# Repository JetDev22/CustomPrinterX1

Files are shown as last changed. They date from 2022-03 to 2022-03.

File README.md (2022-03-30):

# CustomPrinter X1
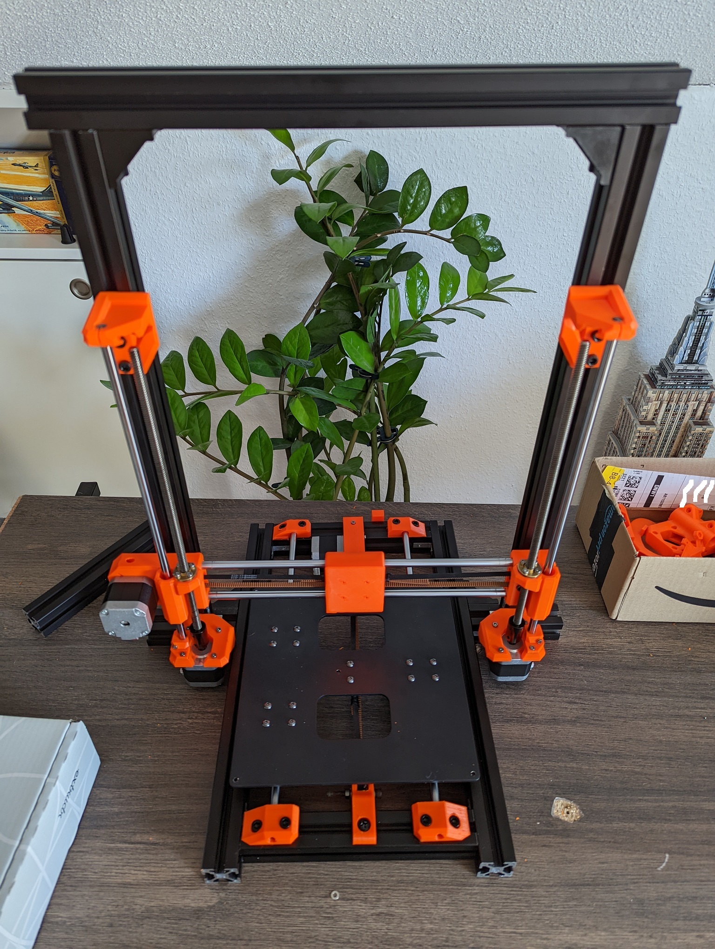
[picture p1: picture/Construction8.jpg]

## The Idea

My Anycubic Mega S was performing quite well for two years, when I suddenly had several kill calls by the firmware due to thermal runaway. I could not isolate the problem. I changed the thermister, heater cartridge, checked the cables .... no change. Sometimes it printed flawless for weeks, other times it stalled several times a day.

So I decided to strip the Mega S for its parts and try to start from scratch, by building my own 3D Printer. The goals where:
- Upgrade to a 32bit board
- Construct a 3030 aluminium extrusion frame, that are intentinally not cut to exact lengths, so the can be used later on
- Add an all metal V6 style Hotend to be able to experiment beyond PETG
- Add a TFT35 display to be able to use the retro-style marlin display, as well as the TFT35 GUI (and customize the GUI)
- Configure Marlin from scratch, to learn more about the firmware and have it fit my printer
- Initially use parts from prusaprinters/thingiverse and replace them, once that printer works reliable, with parts designed by me
- Publish my firmware/parts/ideas/findings on my github to encourage others to do the same or recreate my build

## Parts used from the Anycubic Mega S

The following lists all the parts I reused from disassembling the Mega S:
- Both Z-Axis Nema 17s
- The shorter Extruder NEMA 17
- Both Nema 17s with fixed toothed wheel
- Both 8mm linear rods
- Both 8mm lead screws + lead screw idlers
- Both idler wheels (x axis and heatbed)
- Heatbed (carrier and heatbed itself)
- 12V PSU
- Radial fan from part cooler

## Parts bought to replace / upgrade
- Bigtreetech TFT35 E3 (initially wanted to use the TFT35 V3, but pirces where to high)
- Bigtreetech SKR 2.0 Rev B
- Bightreetech TMC2208
- V6 All Metal Clone (12V)
- PEI coated build plate
- BMG Extruder
- Capricorn PTFE Tube
- Noctua 120mm / 40mm fan
- 2 x 100mm 3030 extrusions
- 3 x 200mm 3030 extrusions
- 3 x 400mm 3030 extrusions
- 2 x 500mm 3030 extrusions
- Nut 8 inline 3030 extrusion angles/mounts
- 2mm pitch belts
- 16AWG Silicon wire
- 4 Core LED Wire 
- JST Connector Set
- JST-SM Connector Set

## Printed Parts from thingiverse / prusaprinters
- [Z-Motor Mount, Z Top Mount, X Motor Mount, X Idler Mount, Y Rod Mounts](https://www.thingiverse.com/thing:2686588/files)
- [V6 Bowden Mount](https://www.thingiverse.com/thing:2023947)
- [V6 Bowden Mount 40mm Hotend Fan Mod](https://www.thingiverse.com/thing:4131521)
- [X Axis Carriage](https://www.thingiverse.com/thing:2514659)
- [PSU Mount for 3030 Frame](https://www.thingiverse.com/thing:4222489/files)

## Printed parts designed by me
- [SKR 2 Rev B Case for 3030 Frame](https://github.com/JetDev22/CustomPrinterX1/blob/main/STLs/SKRCase.stl)
- [SKR 2 Case Top with 120mm Fan mount](https://github.com/JetDev22/CustomPrinterX1/blob/main/STLs/SKRCaseTop.stl)
- [3030 Y Endstop Mount](https://github.com/JetDev22/CustomPrinterX1/blob/main/STLs/YEndstop.stl)
- [3030 Y Motor Mount](https://github.com/JetDev22/CustomPrinterX1/blob/main/STLs/YMotor.stl)

## Marlin Configuration General
- Hotend Thermistor 13 (Hisens up to 300°C - for "Simple ONE" & "All In ONE" hotend - beta 3950, 1%) (in configuration.h)
- Heatbed Thermistor 1 (EPCOS - Best choice for EPCOS thermistors) (in configuration.h)
- Print Dimensions - TBA (in configuration.h)
- Adjusted Extruder EO Steps to 385 for BMG Extruder (in configuration.h)
- Redefined preheat values (PLA 210°C/60°C and PETG 240°C/70°C) (in configuration.h)
- SDSUPPORT (in configuration.h)
- TMC_DEBUG (in configuration_adv.h)
- WATCH_TEMP_PERIOD set to 90 seconds for the hotend if it fluctuates by 2 degress to ease thermal runaway sensitivity (in configuration_adv.h)
- WATCH_BED_TEMP_PERIOD set to 120 seconds for the hotend if it fluctuates by 2 degress to ease thermal runaway sensitivity (in configuration_adv.h)
- USE_CONTROLLER_FAN enabled to start Board Fan whenever the steppers are active, to cool stepper drivers (in configuration_adv.h)
- HOTEND_IDLE_TIMEOUT enabled to avoid preheating to long without starting an actual print, so the filament does not char in the hotend (in configuration_adv.h)
- define NUM_Z_STEPPER_DRIVERS 2 (in configuration_adv.h)
- MESH_BED_LEVELING (in configuration.h)

## Marlin Configuration required for BTT TFT35 E3

For current Bigtreetech published Marlin Settings on TFT35 go [-> HERE](https://github.com/bigtreetech/BIGTREETECH-TouchScreenFirmware#marlin-dependencies)

General options which MUST be activated:

- EEPROM_SETTINGS (in Configuration.h)
- REPRAP_DISCOUNT_FULL_GRAPHIC_SMART_CONTROLLER (in Configuration.h)
- BABYSTEPPING (in Configuration_adv.h)
- AUTO_REPORT_TEMPERATURES (in Configuration_adv.h)
- AUTO_REPORT_POSITION (in Configuration_adv.h)
- M115_GEOMETRY_REPORT (in Configuration_adv.h)
- M114_DETAIL (in Configuration_adv.h)
- REPORT_FAN_CHANGE (in Configuration_adv.h)

Options to support printing from onboard media:

- SDSUPPORT (in Configuration.h)
- LONG_FILENAME_HOST_SUPPORT (in Configuration_adv.h)
- AUTO_REPORT_SD_STATUS (in Configuration_adv.h)
- SDCARD_CONNECTION ONBOARD (in Configuration_adv.h)

Options to support dialog with host:

- EMERGENCY_PARSER (in Configuration_adv.h)
- SERIAL_FLOAT_PRECISION 4 (in Configuration_adv.h)
- HOST_ACTION_COMMANDS (in Configuration_adv.h)
- HOST_PROMPT_SUPPORT (in Configuration_adv.h)

Options to support M600 with host & (Un)Load menu:

- NOZZLE_PARK_FEATURE (in Configuration.h)
- ADVANCED_PAUSE_FEATURE (in Configuration_adv.h)
- PARK_HEAD_ON_PAUSE (in Configuration_adv.h)
- FILAMENT_LOAD_UNLOAD_GCODES (in Configuration_adv.h)

Options to fully support Bed Leveling menu (manual only):

- G26_MESH_VALIDATION (in Configuration.h)

## Marlin Configuration required for SKR 2 Rev B

For current Bigtreetech published Marlin Settings on SKR 2 go [-> HERE](https://3dwork.io/en/complete-guide-skr2/#Firmwares_Marlin)

- SERIAL_PORT 1 (in Configuration.h)
- BAUDRATE 115200 (in Configuration.h)
- SERIAL_PORT_2 -1 (in Configuration.h)
- SERIAL_PORT_3 3 (in Configuration.h)
- PIDTEMP (in Configuration.h)
- PIDTEMPBED (in Configuration.h)
- S_CURVE_ACCELERATION (in Configuration.h)
- EEPROM_SETTINGS (in Configuration.h)
- EEPROM_CHITCHAT (in Configuration.h)
- INDIVIDUAL_AXIS_HOMING_MENU (in Configuration.h)
- LONG_FILENAME_HOST_SUPPORT (in Configuration_adv.h)
- SCROLL_LONG_FILENAMES (in Configuration_adv.h)
- SDCARD_CONNECTION LCD (in Configuration_adv.h)
- E0_AUTO_FAN_PIN FAN1_PIN FAN1 // Assigned to the Hotend (in Configuration_adv.h)
- USE_CONTROLLER_FAN (in Configuration_adv.h)
- CONTROLLER_FAN_PIN FAN2_PIN // FAN2 Assigned to electronics (in Configuration_adv.h)
- CONTROLLER_FAN_EDITABLE (in Configuration_adv.h)
- CONTROLLER_FAN_MENU (in Configuration_adv.h)
- BABYSTEPPING (in Configuration_adv.h)
- DOUBLECLICK_FOR_Z_BABYSTEPPING (in Configuration_adv.h)
- BABYSTEP_ALWAYS_AVAILABLE (in Configuration_adv.h)
- ARC_SUPPORT (in Configuration_adv.h)
- ADVANCED_PAUSE_FEATURE (in Configuration_adv.h)
- CHOPPER_TIMING CHOPPER_DEFAULT_12V (in Configuration_adv.h)
- MONITOR_DRIVER_STATUS (in Configuration_adv.h)
- HYBRID_THRESHOLD (in Configuration_adv.h)
- X_HYBRID_THRESHOLD 100 (in Configuration_adv.h)
- Y_HYBRID_THRESHOLD 100 (in Configuration_adv.h)
- Z_HYBRID_THRESHOLD 15 // default is 4 (in Configuration_adv.h)
- TMC_DEBUG (in Configuration_adv.h)

## Custom Start Gcode

G90 ; use absolute coordinates
M83 ; extruder relative mode
M204 S[machine_max_acceleration_extruding] T[machine_max_acceleration_retracting]
M104 S[first_layer_temperature] ; set extruder temp
M140 S[first_layer_bed_temperature] ; set bed temp
G28 ; home all
M420 S1
G1 Y1.0 Z0.3 F1000 ; move print head up
M190 S[first_layer_bed_temperature] ; wait for bed temp
M109 S[first_layer_temperature] ; wait for extruder temp
G92 E0.0
; initial load
G1 X170 E19 F1000
G1 Y1.6
G1 X5.0 E19 F1000
G92 E0.0
; intro line
G1 Y2.0 Z0.2 F1000
G1 X65.0 E9.0 F1000
G1 X105.0 E12.5 F1000
G92 E0.0

## Custom End Gcode

G1 E-1.0 F2100 ; retract
G92 E0.0
G1{if max_layer_z < max_print_height} Z{z_offset+min(max_layer_z+30, max_print_height)}{endif} E-34.0 F720 ; move print head up & retract filament
G4 ; wait
M104 S0 ; turn off temperature
M140 S0 ; turn off heatbed
M107 ; turn off fan
G1 X0 Y105 F3000 ; park print head
M84 ; disable motors

## PrusaSlicer Setting

TBA

## RepetierServer Settings

TBA

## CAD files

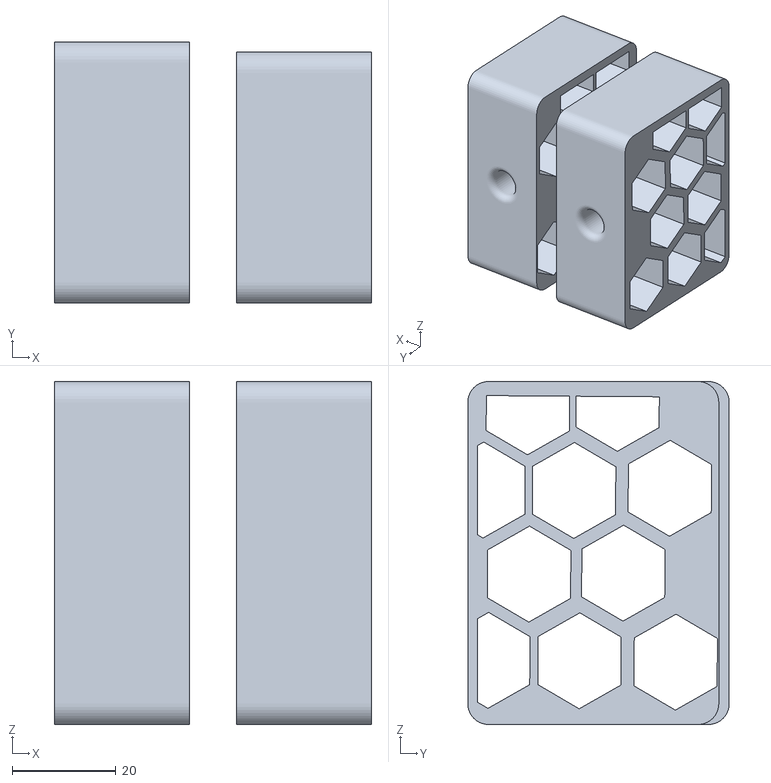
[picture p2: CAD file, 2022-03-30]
STLs/Support.stl
61.0 x 50.3 x 66.0

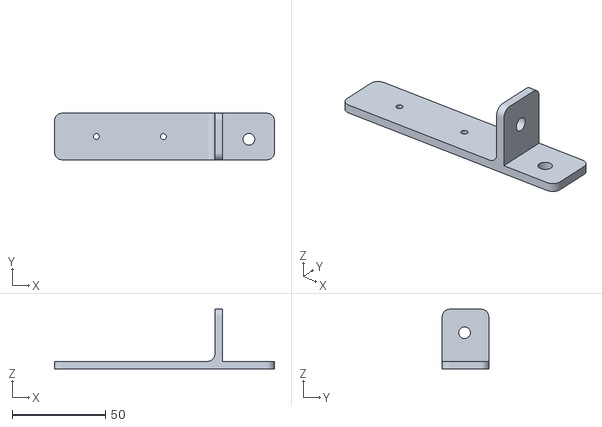
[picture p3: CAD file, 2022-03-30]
STLs/TFTMount.stl
118.1 x 25.0 x 32.0

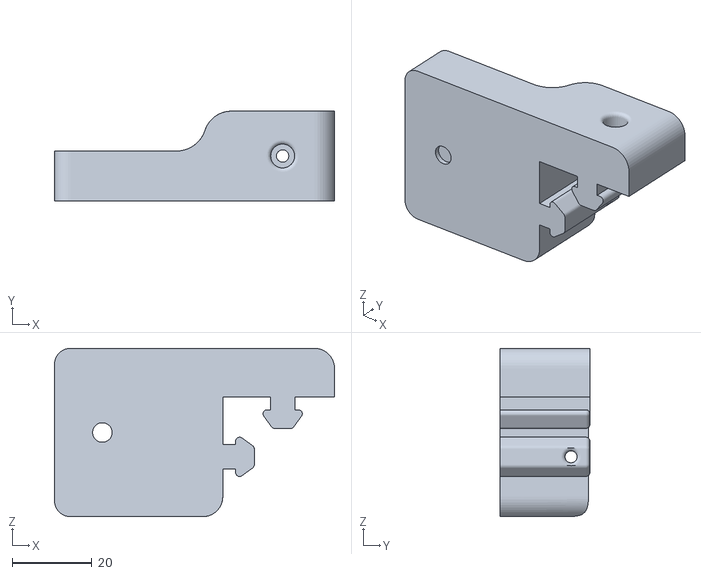
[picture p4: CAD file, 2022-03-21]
STLs/YMotor.stl
70.2 x 22.5 x 42.2

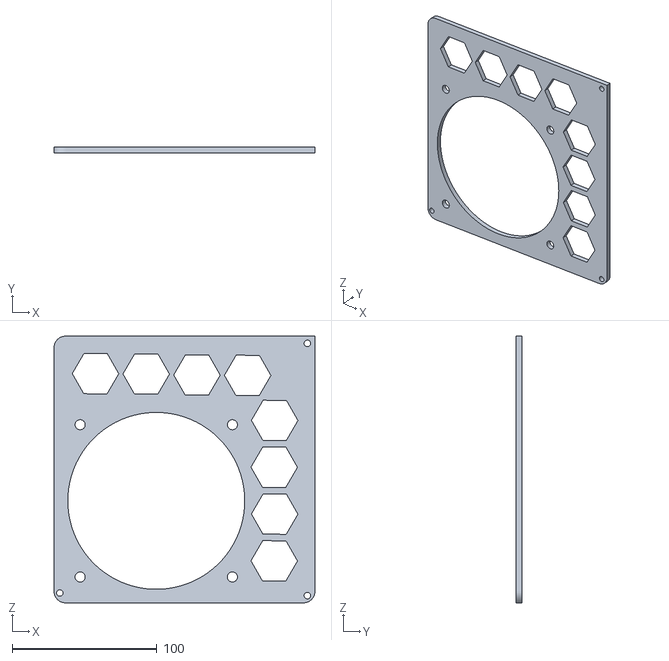
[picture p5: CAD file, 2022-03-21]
STLs/SKRCaseTop.stl
180.0 x 4.00 x 184.0

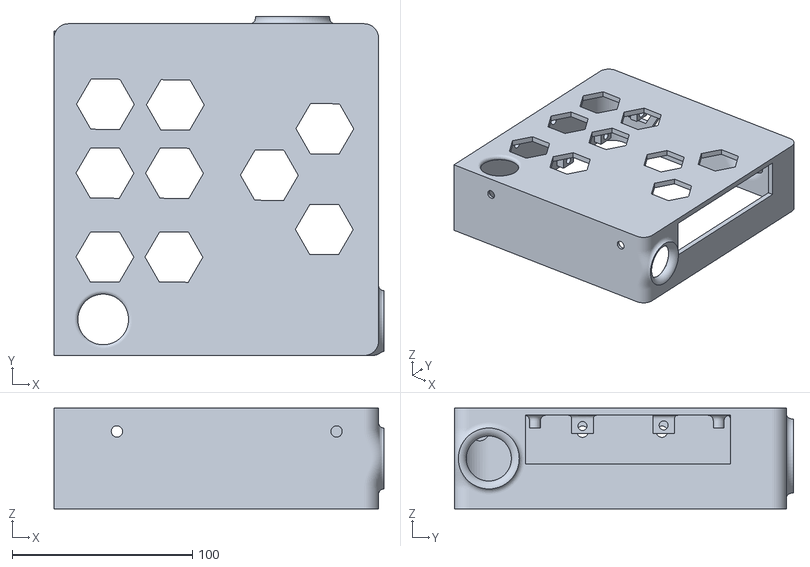
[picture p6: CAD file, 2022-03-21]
STLs/SKRCase.stl
183.0 x 188.0 x 56.0

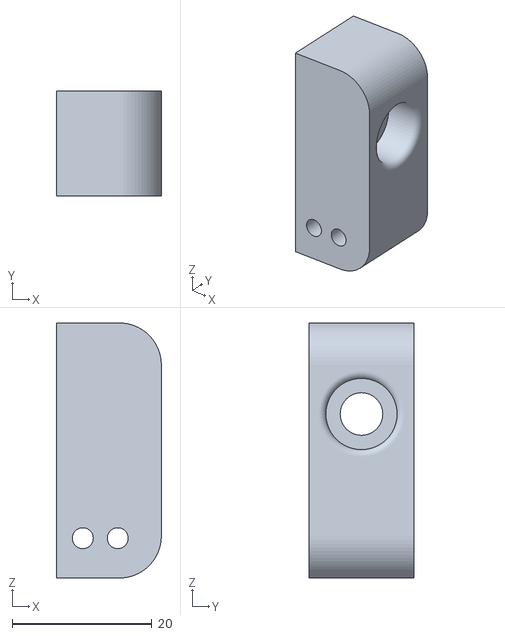
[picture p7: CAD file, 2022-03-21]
STLs/YEndstop.stl
15.0 x 15.0 x 36.5

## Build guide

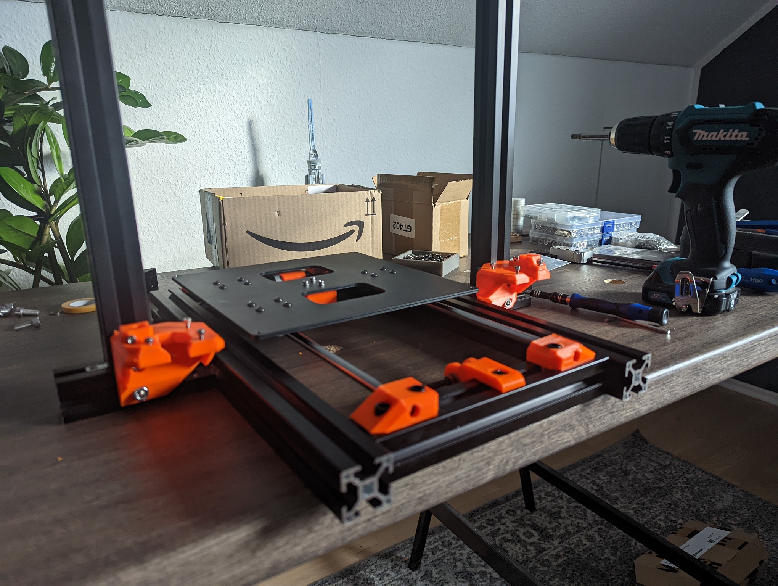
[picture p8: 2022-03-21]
picture/Construction7.jpg

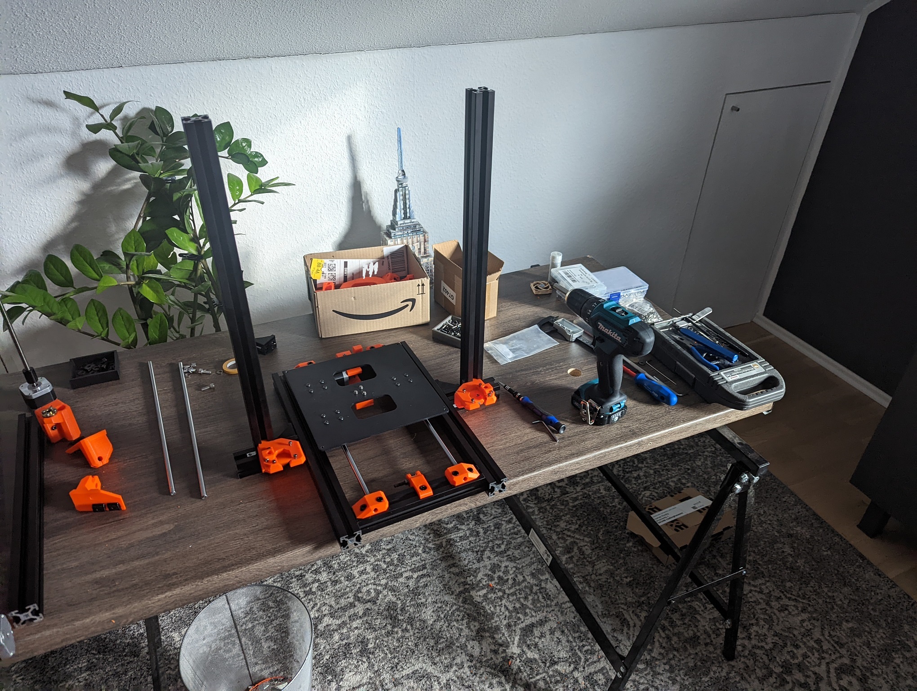
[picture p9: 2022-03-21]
picture/Construction5.jpg

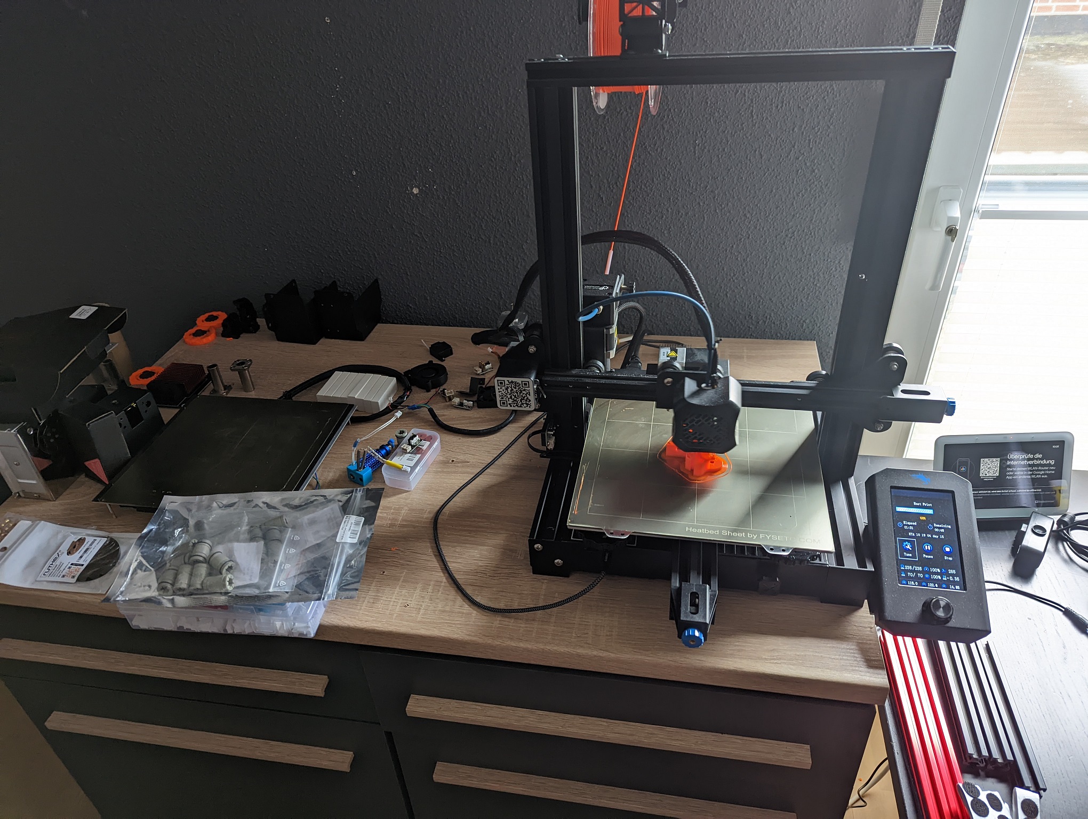
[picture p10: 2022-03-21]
picture/Construction3.jpg

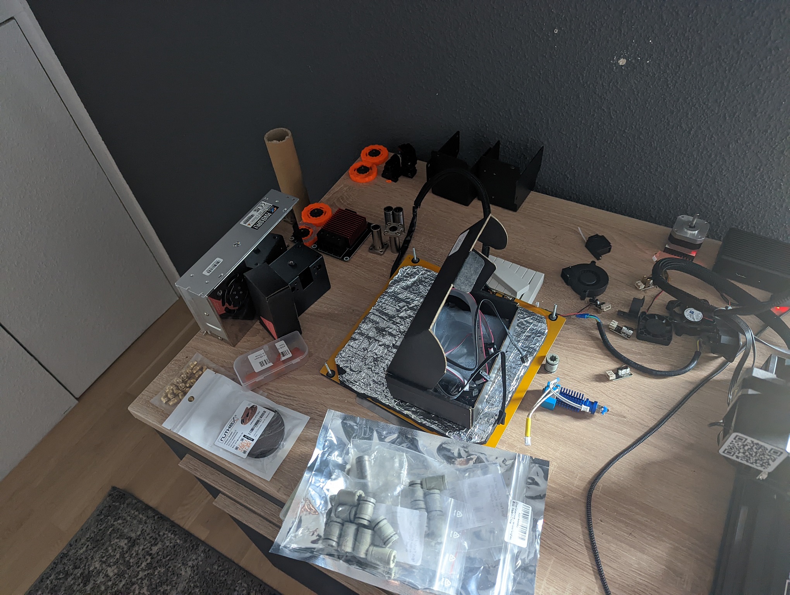
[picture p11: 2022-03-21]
picture/Construction6.jpg

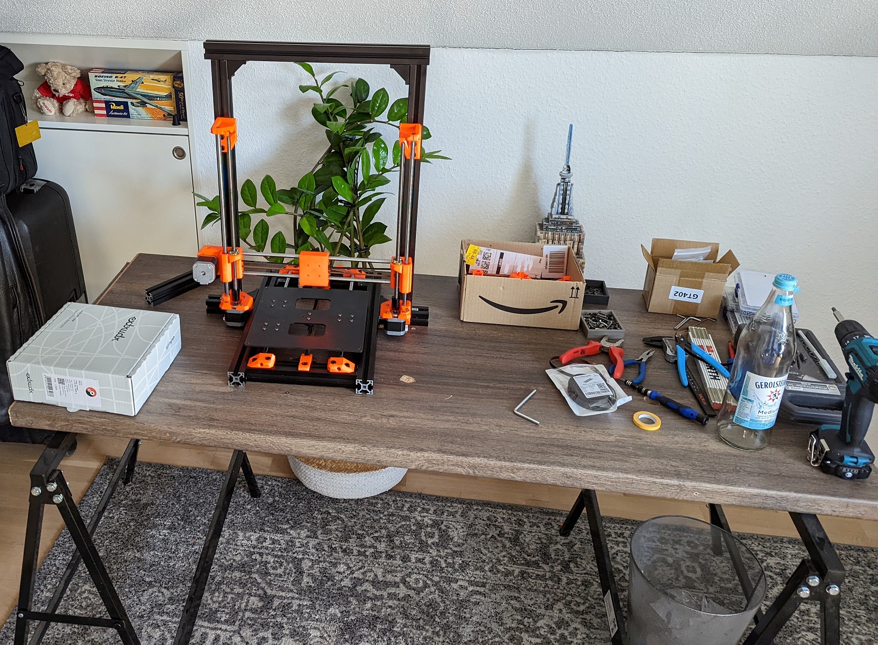
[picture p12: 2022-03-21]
picture/Construction2.jpg

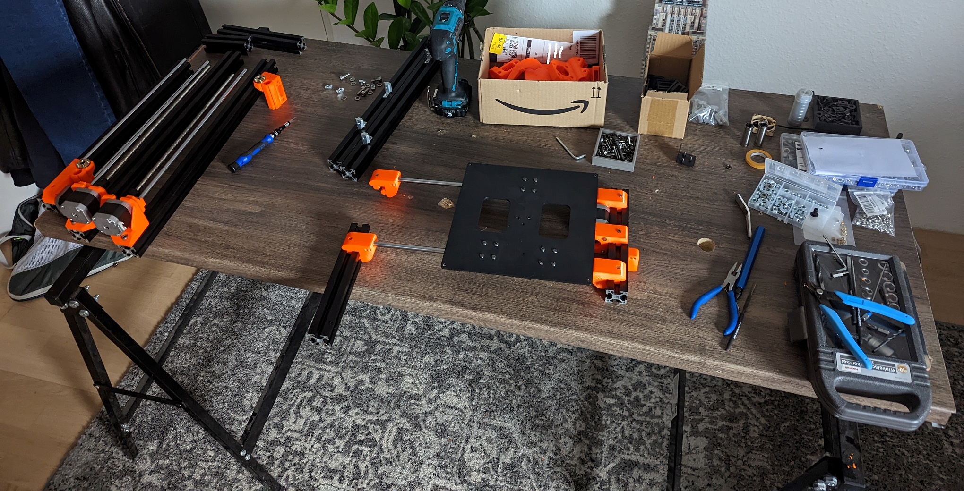
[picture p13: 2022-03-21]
picture/Construction1.jpg

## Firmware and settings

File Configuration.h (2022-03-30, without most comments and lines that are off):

#pragma once
#define CONFIGURATION_H_VERSION 02000903
#define STRING_CONFIG_H_AUTHOR "Wotan X1 Firmware by JetDev22" // Who made the changes.
#define SHOW_BOOTSCREEN
  #define MOTHERBOARD BOARD_BTT_SKR_V2_0_REV_B
#define SERIAL_PORT 1
#define BAUDRATE 115200
#define SERIAL_PORT_2 -1
#define SERIAL_PORT_3 3
#define CUSTOM_MACHINE_NAME "Wotan X1"
#if LINEAR_AXES >= 4
  #define AXIS4_NAME 'A' // :['A', 'B', 'C', 'U', 'V', 'W']
#endif
#if LINEAR_AXES >= 5
  #define AXIS5_NAME 'B' // :['A', 'B', 'C', 'U', 'V', 'W']
#endif
#if LINEAR_AXES >= 6
  #define AXIS6_NAME 'C' // :['A', 'B', 'C', 'U', 'V', 'W']
#endif
#define EXTRUDERS 1
#define DEFAULT_NOMINAL_FILAMENT_DIA 1.75
#define TEMP_SENSOR_0 13
#define TEMP_SENSOR_1 0
#define TEMP_SENSOR_2 0
#define TEMP_SENSOR_3 0
#define TEMP_SENSOR_4 0
#define TEMP_SENSOR_5 0
#define TEMP_SENSOR_6 0
#define TEMP_SENSOR_7 0
#define TEMP_SENSOR_BED 1
#define TEMP_SENSOR_PROBE 0
#define TEMP_SENSOR_CHAMBER 0
#define TEMP_SENSOR_COOLER 0
#define TEMP_SENSOR_BOARD 0
#define TEMP_SENSOR_REDUNDANT 0
#define DUMMY_THERMISTOR_998_VALUE  25
#define DUMMY_THERMISTOR_999_VALUE 100
#define TEMP_RESIDENCY_TIME         10  // (seconds) Time to wait for hotend to "settle" in M109
#define TEMP_WINDOW                  1  // (°C) Temperature proximity for the "temperature reached" timer
#define TEMP_HYSTERESIS              3  // (°C) Temperature proximity considered "close enough" to the target
#define TEMP_BED_RESIDENCY_TIME     10  // (seconds) Time to wait for bed to "settle" in M190
#define TEMP_BED_WINDOW              1  // (°C) Temperature proximity for the "temperature reached" timer
#define TEMP_BED_HYSTERESIS          3  // (°C) Temperature proximity considered "close enough" to the target
#define TEMP_CHAMBER_RESIDENCY_TIME 10  // (seconds) Time to wait for chamber to "settle" in M191
#define TEMP_CHAMBER_WINDOW          1  // (°C) Temperature proximity for the "temperature reached" timer
#define TEMP_CHAMBER_HYSTERESIS      3  // (°C) Temperature proximity considered "close enough" to the target
#if TEMP_SENSOR_REDUNDANT
  #define TEMP_SENSOR_REDUNDANT_SOURCE    E1  // The sensor that will provide the redundant reading.
  #define TEMP_SENSOR_REDUNDANT_TARGET    E0  // The sensor that we are providing a redundant reading for.
  #define TEMP_SENSOR_REDUNDANT_MAX_DIFF  10  // (°C) Temperature difference that will trigger a print abort.
#endif
#define HEATER_0_MINTEMP   5
#define HEATER_1_MINTEMP   5
#define HEATER_2_MINTEMP   5
#define HEATER_3_MINTEMP   5
#define HEATER_4_MINTEMP   5
#define HEATER_5_MINTEMP   5
#define HEATER_6_MINTEMP   5
#define HEATER_7_MINTEMP   5
#define BED_MINTEMP        5
#define CHAMBER_MINTEMP    5
#define HEATER_0_MAXTEMP 275
#define HEATER_1_MAXTEMP 275
#define HEATER_2_MAXTEMP 275
#define HEATER_3_MAXTEMP 275
#define HEATER_4_MAXTEMP 275
#define HEATER_5_MAXTEMP 275
#define HEATER_6_MAXTEMP 275
#define HEATER_7_MAXTEMP 275
#define BED_MAXTEMP      150
#define CHAMBER_MAXTEMP  60
#define HOTEND_OVERSHOOT 15   // (°C) Forbid temperatures over MAXTEMP - OVERSHOOT
#define BED_OVERSHOOT    10   // (°C) Forbid temperatures over MAXTEMP - OVERSHOOT
#define COOLER_OVERSHOOT  2   // (°C) Forbid temperatures closer than OVERSHOOT
#define PIDTEMP
#define BANG_MAX 255     // Limits current to nozzle while in bang-bang mode; 255=full current
#define PID_MAX BANG_MAX // Limits current to nozzle while PID is active (see PID_FUNCTIONAL_RANGE below); 255=full current
#define PID_K1 0.95      // Smoothing factor within any PID loop
    #define DEFAULT_Kp  22.20
    #define DEFAULT_Ki   1.08
    #define DEFAULT_Kd 114.00
#define PIDTEMPBED
#define MAX_BED_POWER 255 // limits duty cycle to bed; 255=full current
  #define DEFAULT_bedKp 10.00
  #define DEFAULT_bedKi .023
  #define DEFAULT_bedKd 305.4
#define MAX_CHAMBER_POWER 255 // limits duty cycle to chamber heater; 255=full current
  #define PID_FUNCTIONAL_RANGE 10 // If the temperature difference between the target temperature and the actual temperature
#define PREVENT_COLD_EXTRUSION
#define EXTRUDE_MINTEMP 170
#define PREVENT_LENGTHY_EXTRUDE
#define EXTRUDE_MAXLENGTH 200
#define THERMAL_PROTECTION_HOTENDS // Enable thermal protection for all extruders
#define THERMAL_PROTECTION_BED     // Enable thermal protection for the heated bed
#define THERMAL_PROTECTION_CHAMBER // Enable thermal protection for the heated chamber
#define THERMAL_PROTECTION_COOLER  // Enable thermal protection for the laser cooling
#define USE_XMIN_PLUG
#define USE_YMIN_PLUG
#define USE_ZMIN_PLUG
#define ENDSTOPPULLUPS
#define X_MIN_ENDSTOP_INVERTING true // Set to true to invert the logic of the endstop.
#define Y_MIN_ENDSTOP_INVERTING true // Set to true to invert the logic of the endstop.
#define Z_MIN_ENDSTOP_INVERTING true // Set to true to invert the logic of the endstop.
#define I_MIN_ENDSTOP_INVERTING false // Set to true to invert the logic of the endstop.
#define J_MIN_ENDSTOP_INVERTING false // Set to true to invert the logic of the endstop.
#define K_MIN_ENDSTOP_INVERTING false // Set to true to invert the logic of the endstop.
#define X_MAX_ENDSTOP_INVERTING false // Set to true to invert the logic of the endstop.
#define Y_MAX_ENDSTOP_INVERTING false // Set to true to invert the logic of the endstop.
#define Z_MAX_ENDSTOP_INVERTING false // Set to true to invert the logic of the endstop.
#define I_MAX_ENDSTOP_INVERTING false // Set to true to invert the logic of the endstop.
#define J_MAX_ENDSTOP_INVERTING false // Set to true to invert the logic of the endstop.
#define K_MAX_ENDSTOP_INVERTING false // Set to true to invert the logic of the endstop.
#define Z_MIN_PROBE_ENDSTOP_INVERTING false // Set to true to invert the logic of the probe.
#define X_DRIVER_TYPE  TMC2208
#define Y_DRIVER_TYPE  TMC2208
#define Z_DRIVER_TYPE  TMC2208
#define Z2_DRIVER_TYPE TMC2208
#define E0_DRIVER_TYPE TMC2208
#define DEFAULT_AXIS_STEPS_PER_UNIT   { 80, 80, 400, 385 }
#define DEFAULT_MAX_FEEDRATE          { 300, 300, 5, 25 }
#define DEFAULT_MAX_ACCELERATION      { 3000, 3000, 100, 10000 }
#define DEFAULT_ACCELERATION          3000    // X, Y, Z and E acceleration for printing moves
#define DEFAULT_RETRACT_ACCELERATION  3000    // E acceleration for retracts
#define DEFAULT_TRAVEL_ACCELERATION   3000    // X, Y, Z acceleration for travel (non printing) moves
#define DEFAULT_EJERK    5.0  // May be used by Linear Advance
  #define JUNCTION_DEVIATION_MM 0.013 // (mm) Distance from real junction edge
  #define JD_HANDLE_SMALL_SEGMENTS    // Use curvature estimation instead of just the junction angle
#define S_CURVE_ACCELERATION
#define Z_MIN_PROBE_USES_Z_MIN_ENDSTOP_PIN
#define NOZZLE_TO_PROBE_OFFSET { 10, 10, 0 }
#define PROBING_MARGIN 10
#define XY_PROBE_FEEDRATE (133*60)
#define Z_PROBE_FEEDRATE_FAST (4*60)
#define Z_PROBE_FEEDRATE_SLOW (Z_PROBE_FEEDRATE_FAST / 2)
#define Z_CLEARANCE_DEPLOY_PROBE   10 // Z Clearance for Deploy/Stow
#define Z_CLEARANCE_BETWEEN_PROBES  5 // Z Clearance between probe points
#define Z_CLEARANCE_MULTI_PROBE     5 // Z Clearance between multiple probes
#define Z_PROBE_LOW_POINT          -2 // Farthest distance below the trigger-point to go before stopping
#define Z_PROBE_OFFSET_RANGE_MIN -20
#define Z_PROBE_OFFSET_RANGE_MAX 20
#define X_ENABLE_ON 0
#define Y_ENABLE_ON 0
#define Z_ENABLE_ON 0
#define E_ENABLE_ON 0 // For all extruders
#define DISABLE_X false
#define DISABLE_Y false
#define DISABLE_Z false
#define DISABLE_E false             // Disable the extruder when not stepping
#define DISABLE_INACTIVE_EXTRUDER   // Keep only the active extruder enabled
#define INVERT_X_DIR false
#define INVERT_Y_DIR false
#define INVERT_Z_DIR false
#define INVERT_E0_DIR false
#define INVERT_E1_DIR false
#define INVERT_E2_DIR false
#define INVERT_E3_DIR false
#define INVERT_E4_DIR false
#define INVERT_E5_DIR false
#define INVERT_E6_DIR false
#define INVERT_E7_DIR false
#define X_HOME_DIR -1
#define Y_HOME_DIR -1
#define Z_HOME_DIR -1
#define X_BED_SIZE 175
#define Y_BED_SIZE 180
#define X_MIN_POS 0
#define Y_MIN_POS 0
#define Z_MIN_POS 0
#define X_MAX_POS X_BED_SIZE
#define Y_MAX_POS Y_BED_SIZE
#define Z_MAX_POS 200
#define MIN_SOFTWARE_ENDSTOPS
  #define MIN_SOFTWARE_ENDSTOP_X
  #define MIN_SOFTWARE_ENDSTOP_Y
  #define MIN_SOFTWARE_ENDSTOP_Z
  #define MIN_SOFTWARE_ENDSTOP_I
  #define MIN_SOFTWARE_ENDSTOP_J
  #define MIN_SOFTWARE_ENDSTOP_K
#define MAX_SOFTWARE_ENDSTOPS
  #define MAX_SOFTWARE_ENDSTOP_X
  #define MAX_SOFTWARE_ENDSTOP_Y
  #define MAX_SOFTWARE_ENDSTOP_Z
  #define MAX_SOFTWARE_ENDSTOP_I
  #define MAX_SOFTWARE_ENDSTOP_J
  #define MAX_SOFTWARE_ENDSTOP_K
#define MESH_BED_LEVELING
  #define MANUAL_PROBE_START_Z 0.2  // (mm) Comment out to use the last-measured height
  #define ENABLE_LEVELING_FADE_HEIGHT
    #define DEFAULT_LEVELING_FADE_HEIGHT 10.0 // (mm) Default fade height.
  #define SEGMENT_LEVELED_MOVES
  #define LEVELED_SEGMENT_LENGTH 5.0 // (mm) Length of all segments (except the last one)
  #define G26_MESH_VALIDATION
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

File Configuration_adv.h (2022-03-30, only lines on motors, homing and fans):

  #define CONTROLLER_FAN_PIN FAN2_PIN           // Set a custom pin for the controller fan
#define E0_AUTO_FAN_PIN FAN1_PIN
#define E1_AUTO_FAN_PIN -1
#define E2_AUTO_FAN_PIN -1
#define E3_AUTO_FAN_PIN -1
#define E4_AUTO_FAN_PIN -1
#define E5_AUTO_FAN_PIN -1
#define E6_AUTO_FAN_PIN -1
#define E7_AUTO_FAN_PIN -1
#define CHAMBER_AUTO_FAN_PIN -1
#define COOLER_AUTO_FAN_PIN -1
#define COOLER_FAN_PIN FAN_PIN
#define HOMING_BUMP_MM      { 5, 5, 2 }       // (mm) Backoff from endstops after first bump
#define HOMING_BUMP_DIVISOR { 2, 2, 4 }       // Re-Bump Speed Divisor (Divides the Homing Feedrate)
#define MICROSTEP_MODES { 16, 16, 16, 16, 16, 16 } // [1,2,4,8,16]
#define ADVANCED_PAUSE_FEATURE
  #define ADVANCED_PAUSE_PURGE_FEEDRATE        3  // (mm/s) Extrude feedrate (after loading). Should be slower than load feedrate.
  #define ADVANCED_PAUSE_PURGE_LENGTH         50  // (mm) Length to extrude after loading.
  #define ADVANCED_PAUSE_RESUME_PRIME          0  // (mm) Extra distance to prime nozzle after returning from park.
    #define X_CURRENT       800        // (mA) RMS current. Multiply by 1.414 for peak current.
    #define X_CURRENT_HOME  X_CURRENT  // (mA) RMS current for sensorless homing
    #define X_MICROSTEPS     16        // 0..256
    #define Y_CURRENT       800
    #define Y_CURRENT_HOME  Y_CURRENT
    #define Y_MICROSTEPS     16
    #define Z_CURRENT       800
    #define Z_CURRENT_HOME  Z_CURRENT
    #define Z_MICROSTEPS     16
    #define Z2_CURRENT      800
    #define Z2_CURRENT_HOME Z2_CURRENT
    #define Z2_MICROSTEPS    Z_MICROSTEPS
    #define E0_CURRENT      800
    #define E0_MICROSTEPS    16
    #define CURRENT_STEP_DOWN     50  // [mA]
    #define REPORT_CURRENT_CHANGE
  #define HYBRID_THRESHOLD
  #define X_HYBRID_THRESHOLD     100  // [mm/s]
  #define X2_HYBRID_THRESHOLD    100
  #define Y_HYBRID_THRESHOLD     100
  #define Y2_HYBRID_THRESHOLD    100
  #define Z_HYBRID_THRESHOLD      15
  #define Z2_HYBRID_THRESHOLD     15
  #define Z3_HYBRID_THRESHOLD      3
  #define Z4_HYBRID_THRESHOLD      3
  #define I_HYBRID_THRESHOLD       3
  #define J_HYBRID_THRESHOLD       3
  #define K_HYBRID_THRESHOLD       3
  #define E0_HYBRID_THRESHOLD     30
  #define E1_HYBRID_THRESHOLD     30
  #define E2_HYBRID_THRESHOLD     30
  #define E3_HYBRID_THRESHOLD     30
  #define E4_HYBRID_THRESHOLD     30
  #define E5_HYBRID_THRESHOLD     30
  #define E6_HYBRID_THRESHOLD     30
  #define E7_HYBRID_THRESHOLD     30

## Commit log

2022-03-21 first STL upload
    [SKRCase.stl, SKRCaseTop.stl, YEndstop.stl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]
2022-03-21 added Marlin Config
2022-03-21 added marlin changes for TFT35 E3
2022-03-21 added SKR 2 Marlin Config
2022-03-30 added further files
    [Support.stl, TFTMount.stl]
2022-03-30 added Marlin Files
    [Configuration.h, Configuration_adv.h]
2022-03-30 added reprap_discount marlin config
    to enable Marlin Emulation on TFT35

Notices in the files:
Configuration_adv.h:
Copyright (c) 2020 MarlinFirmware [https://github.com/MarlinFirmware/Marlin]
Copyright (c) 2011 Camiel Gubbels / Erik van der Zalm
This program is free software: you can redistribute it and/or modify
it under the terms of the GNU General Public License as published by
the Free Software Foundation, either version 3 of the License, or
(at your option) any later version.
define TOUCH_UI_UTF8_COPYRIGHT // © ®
